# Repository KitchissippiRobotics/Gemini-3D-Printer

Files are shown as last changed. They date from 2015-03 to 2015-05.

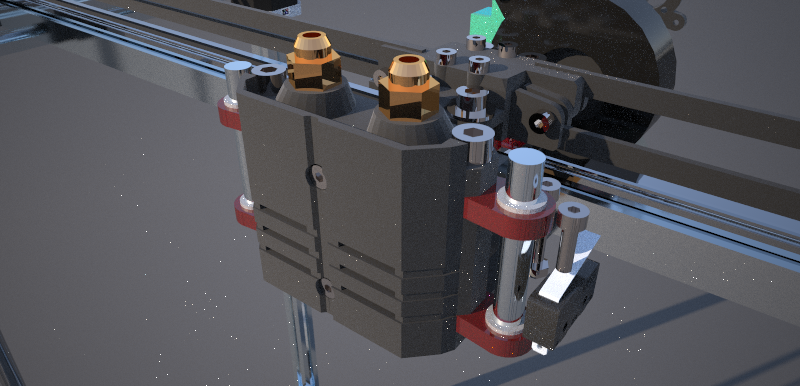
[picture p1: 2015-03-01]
Test Renderings/Development Mockup HA.05.1.png

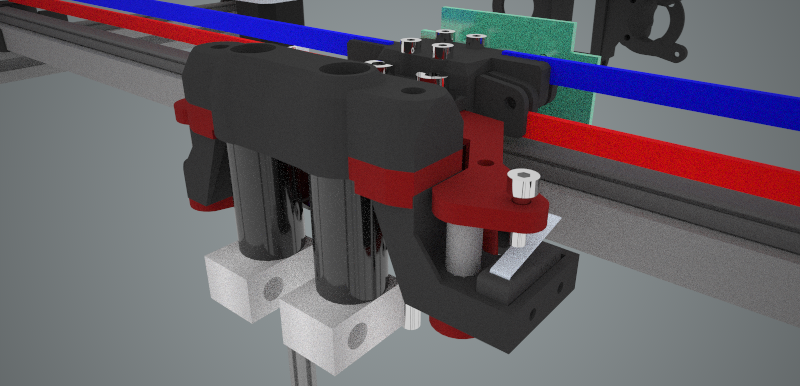
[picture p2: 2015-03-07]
Test Renderings/Development Mockup - Proof of Concept Preview.png

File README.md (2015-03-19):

# Gemini-3D-Printer
<h1>CoreXY RepRap Style 3D Printer</h1>

This is a test bed for experiments aiming for a large 300mm X 300mm X 400+mm print area FFF (layered filament) 3D printer.

<h2>Project Status and Description</h2>

This is an in-progress design for the machine - the source may change frequently and is not currently stable.
Any questions can be directed to novakane on the freenode IRC channel #reprap 

Initial object models were designed to minimize initial print time; test the underlying design theory; and finally, identify stress points in assembly.
This makes the parts more fragile than a production model, however the initial K02.2 prototype successfully made several prints of decent quality.
Most print failures may have been explained by early bed mounting and filament pusher mounting - these were done mostly as hacks to test the electronics and basic mechanism.

<h2>History Notes</h2>

This project is the developers second CoreXY design and 5th original 3D printer design.

- The first version - several revisions of the K02.1 - was based around an experimental carriage for movement using low cost materials
- The first version was abandoned due to required materials being made of large lengths of steel; while fully functional, the machine was heavier than ideal
- Carriages formed the basis of the successful K03.1 and K03.2 prototype delta machines, intended as outlets for recycling initial K02 materials, fully functional but incomplete at this writing.
- Cost analysis revealed that the original K02 (and perhaps K03) was not providing significant savings in cost vs production effort 
- production of the K02/K03 machines accurately requires machinery exceeding any savings - they can be built with simple tools like a punch/hand-drill/hacksaw, but great care must be taken (mass replication would be difficult)

<h2>Work Notes</h2>

This project is the developers second CoreXY design and 5th original 3D printer design.

- The first version - several revisions of the K02.1 - was based around an experimental carriage for movement using low cost materials
- The first version was abandoned due to required materials being made of steel; while fully functional, the machine was heavier than ideal
- Carriages formed the basis of the successful K03.1 and K03.2 prototype delta machines, intended as outlets for recycling initial K02 materials, fully functional but incomplete at this writing.
- Cost analysis revealed that the original K02 (and perhaps K03) was not providing significant savings in cost vs production effort 
- production of the K02/K03 machines accurately requires machinery exceeding any savings - they can be built with simple tools like a punch/hand-drill/hacksaw, but great care must be taken (mass replication would be difficult)

<h2>Development Notes</h2>

*19/March/2015* Hotend Chassis now merged into the Master. Starting work on finalizing rest of X carriage.

<h2>Incomplete BOM</h2>

<h3>Hardware and Electronics</h3>

<h2>Incomplete BOM</h2>

- (5) 20mm X 20mm x 500mm aluminum slotted extrusions (20x20 at half meter lengths) for horizontal dimensions
- (4) 1000mm for vertical segments {(4) 250mm length cut from ends to form part of the base
- (16) F694ZZ bearings for idlers
- (2) GT2-20 pulleys for drive motors
- (2) 50:1 geared NEMA17 motors for extruder pusher
- (2) 8mm ID x 13mm OD hobbed pulley with groove
- (4) Pneumatic pushfit connectors
- (2) ?? length of PTFE Tube 2mm ID x 4mm OD for bowden drive
- (4) 12mm x 500mm hardened steel rod for Z axis linear guide
- (4) LM12UU bearings for Z axis linear guide
_ (150?) M4x10mm allen head steel bolts
- (100?) M3x10mm allen head steel bolts
- (2) M4x?? hex head bolts for Y axis idlers
- (2) M4x?? hex head bolts for Y axis idlers
- (4) M4x50mm allen head steel bolts for Hotend Assembly mount to X Carriage
- (3) MGR9 x 500mm linear rails for CoreXY linear guides
- (3) micro switches for endstops
- (1) 24v 15A 360W power supply
- (1) Smoothieboard for controller
- (2) 12v 0.1A 25mm DC fan for bent cooling on hotends
- (2) jhead hotends 0.4mm nozzle
- (1) 12v 0.06A blower fan

<h2>Voltage converters for inputs to controller from 24v PSU</h2>

24v in - heatbed, hotends, motors
12v in - fans in Hotend assembly / X Carriage / Electronics Assembly (keep under 2 amp)
5v  in - USB/ethernet/CPU power (USB equivalent draw) (keep under 1 amp)

<h2>About the Developer</h2>

- "I am not an engineer, but I play one on the Internet"
- I have played many roles in my life, I am a software developer, an artist, an animator, a musician, a labourer, a technical analyst, a network engineer, an electronics engineer, an educator, a lover, a fighter.
- I am a jack of all trades, a traveller of life and today - I am a roboticist.
- I can be found on #reprap IRC as "novakane"
- I am attempting to bring together what little I know of mechanics, assembly, and avionics into a cohesive 3D printing platform

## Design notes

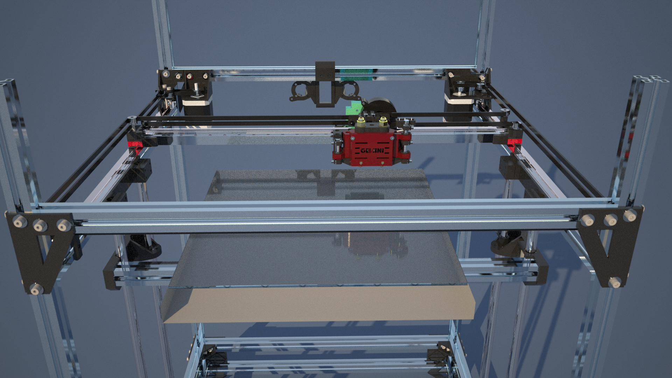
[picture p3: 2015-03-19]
Test Renderings/Development Mockup - Overview.png

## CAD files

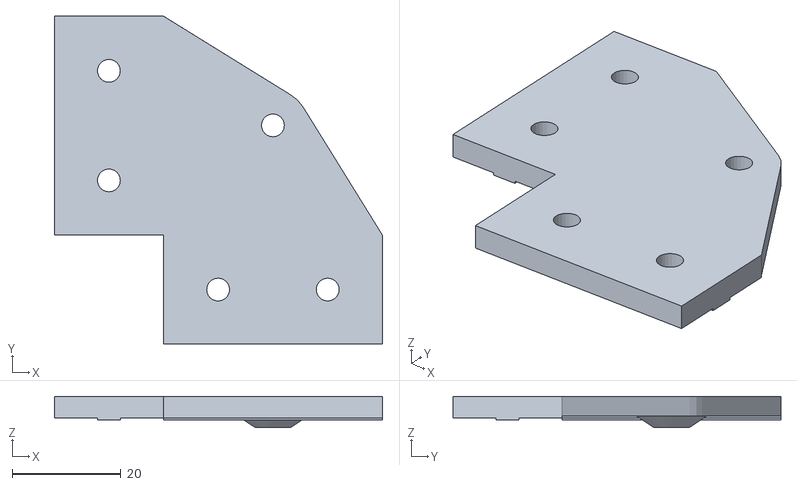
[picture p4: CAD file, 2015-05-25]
Print Models/Top Idler Corner.stl
60.3 x 60.3 x 5.79

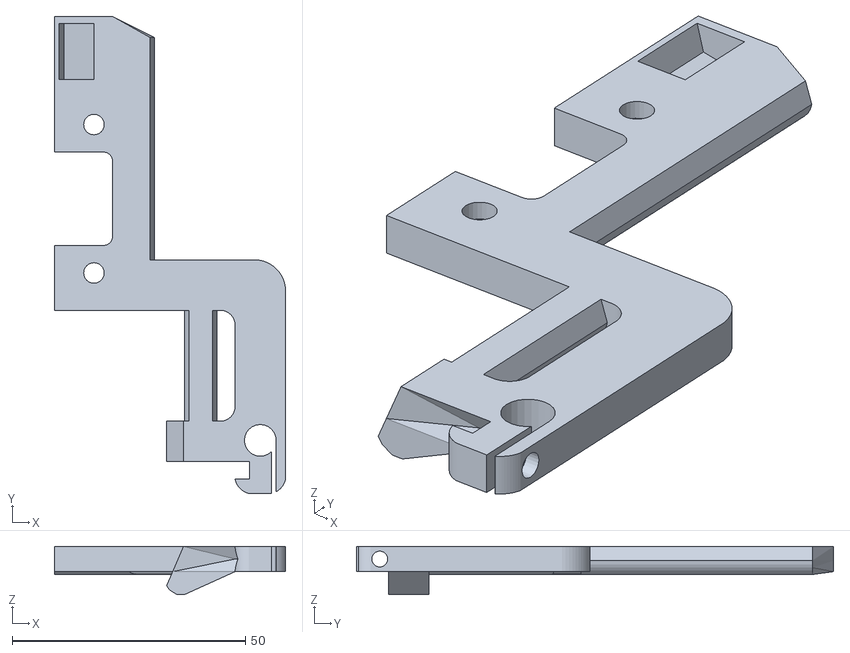
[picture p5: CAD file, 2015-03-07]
Test Models/Ducted Base Test.stl
49.5 x 102.2 x 10.3

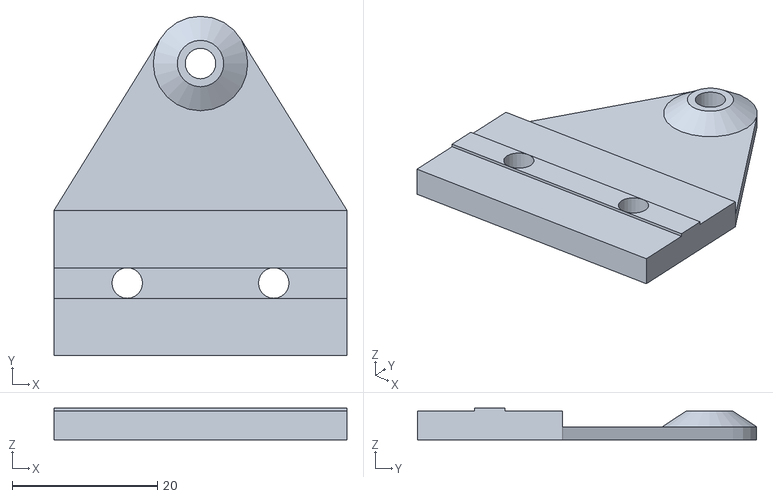
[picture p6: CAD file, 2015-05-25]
Print Models/Bottom Idler Corner.stl
40.3 x 46.7 x 4.40

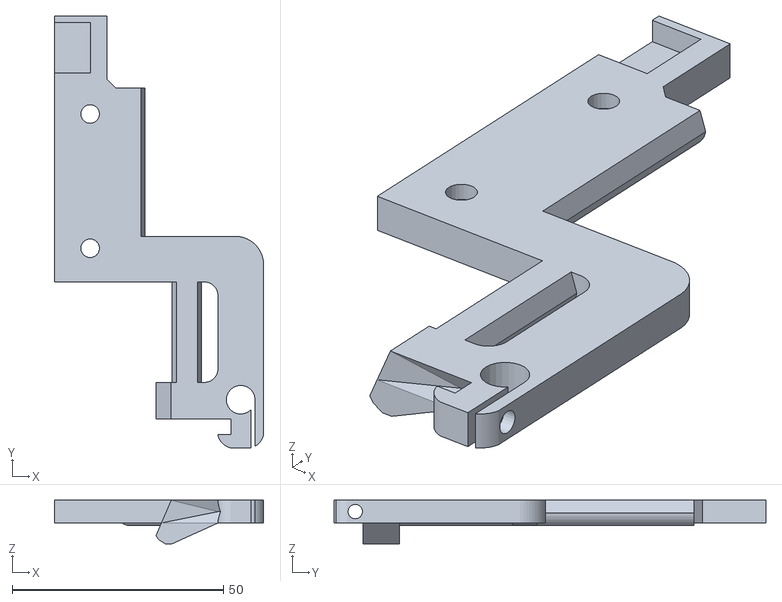
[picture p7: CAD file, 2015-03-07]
Test Models/Development Mockup.stl
49.5 x 102.2 x 10.3

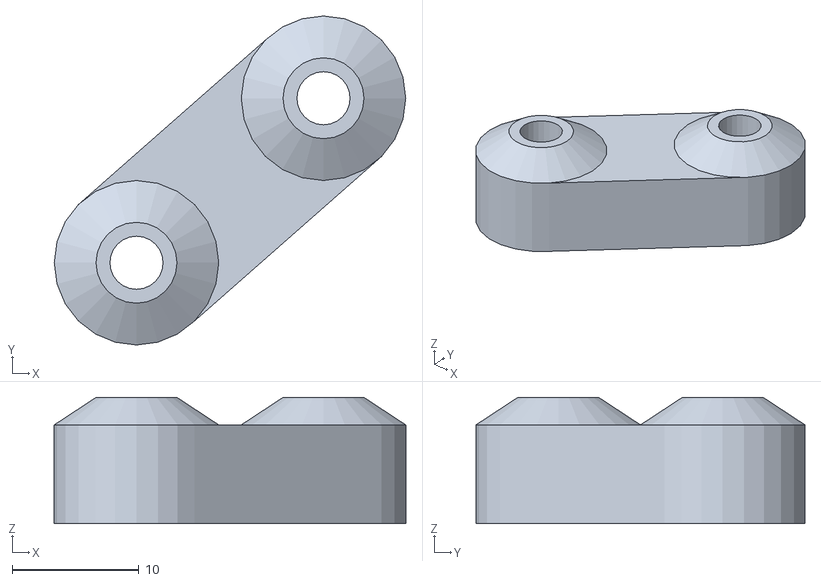
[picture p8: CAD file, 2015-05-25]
Print Models/X End - Pulley Support (x2).stl
27.8 x 26.0 x 9.97

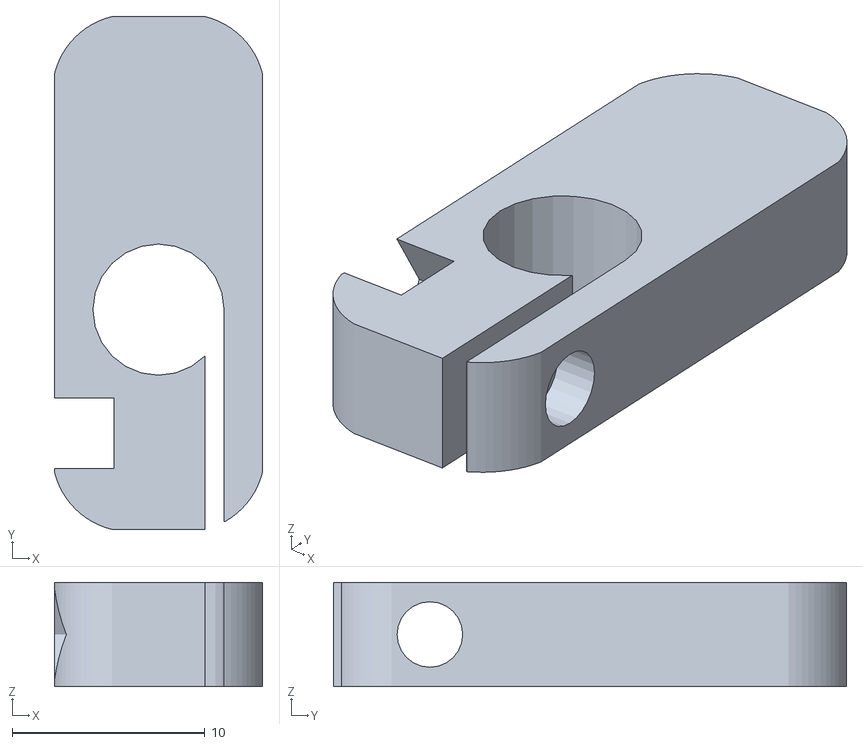
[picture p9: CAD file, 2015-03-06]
Test Models/Clamp.stl
10.8 x 26.6 x 5.40

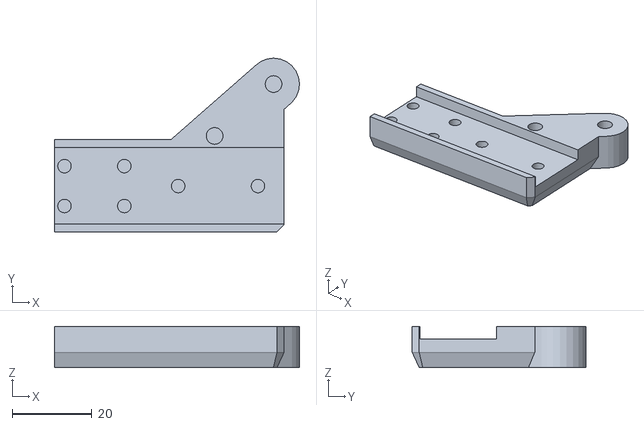
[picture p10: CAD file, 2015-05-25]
Print Models/X End - Left Base.stl
61.4 x 43.5 x 10.3

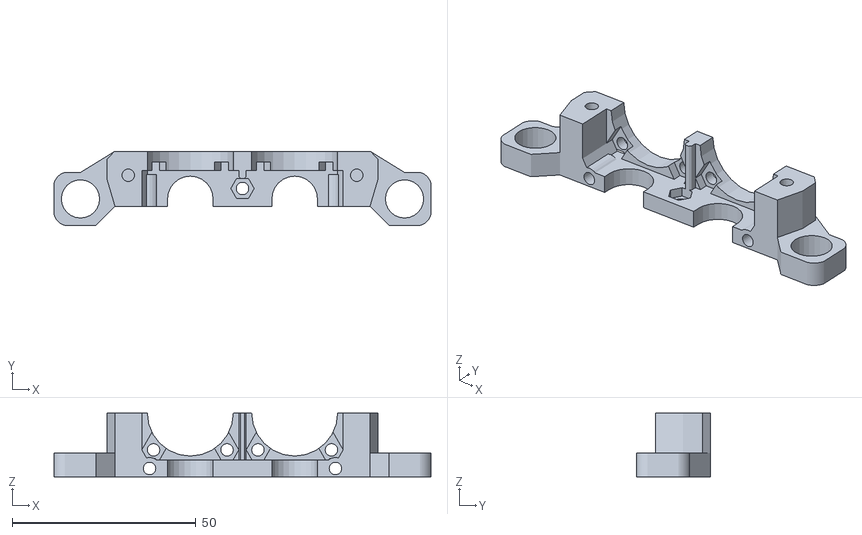
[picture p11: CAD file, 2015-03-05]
Test Models/Beefcake Mount.stl
102.6 x 20.1 x 17.4

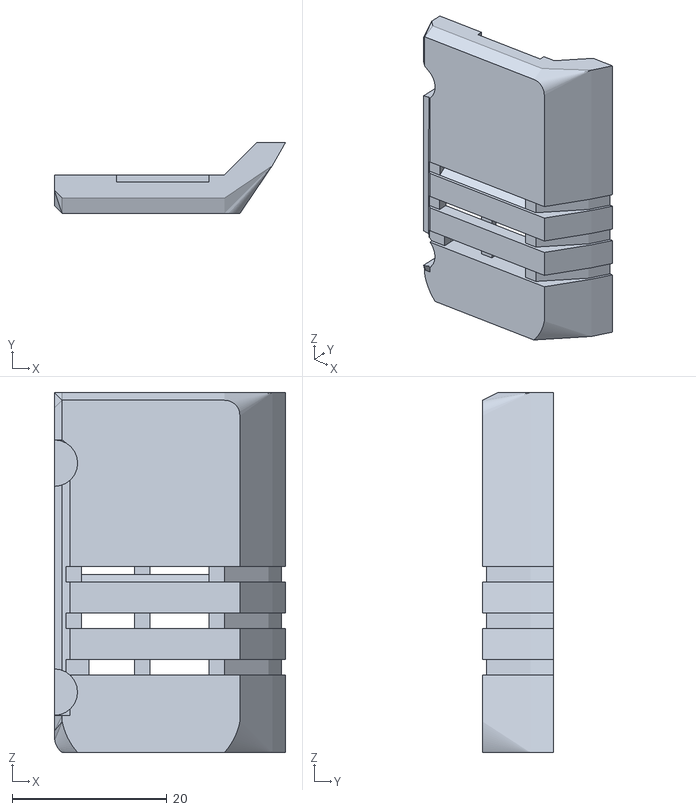
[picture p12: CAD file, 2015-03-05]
Test Models/Vent Cover.stl
29.9 x 9.19 x 46.5

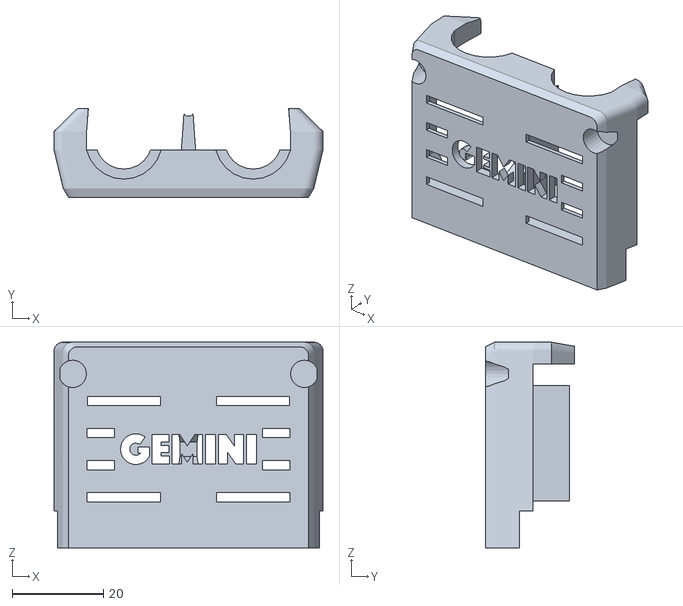
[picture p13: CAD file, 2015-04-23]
Print Models/Hotend Chassis - Groovemount Cover.stl
58.8 x 19.4 x 44.9

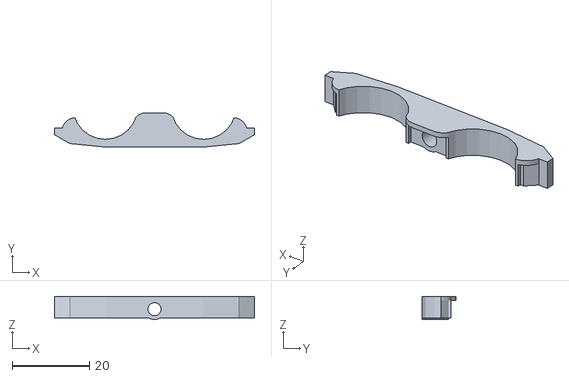
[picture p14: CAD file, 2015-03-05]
Test Models/HA Lower Clamp.stl
51.9 x 8.86 x 6.00

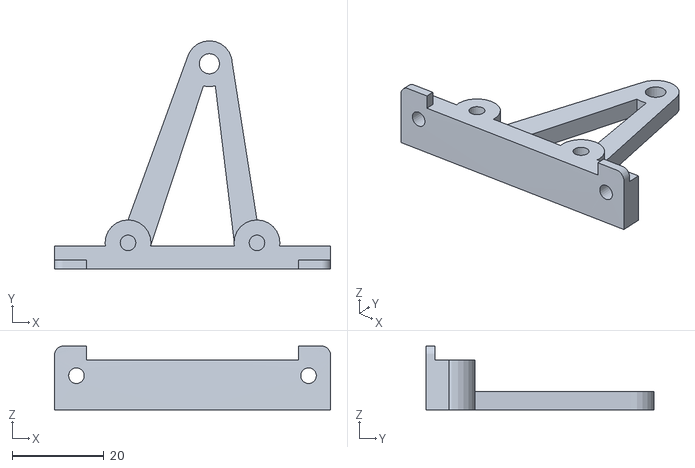
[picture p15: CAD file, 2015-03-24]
Print Models/X Carriage - Terminal Mount.stl
60.0 x 49.7 x 13.9

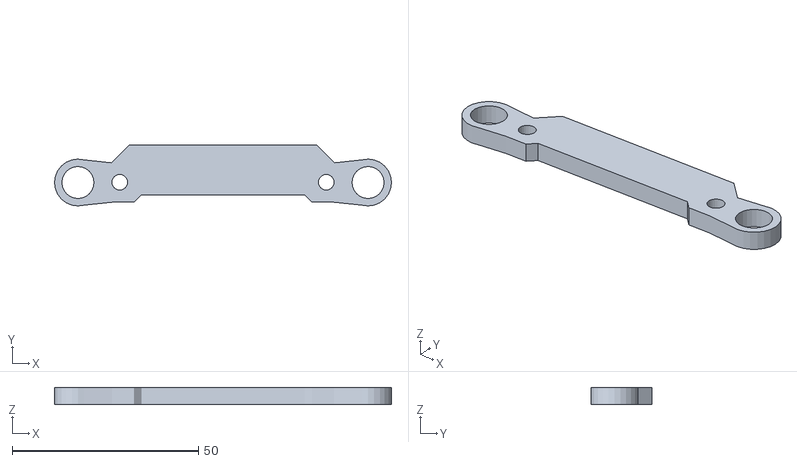
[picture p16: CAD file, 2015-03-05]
Test Models/HA Cross Bar.stl
90.6 x 16.4 x 4.60

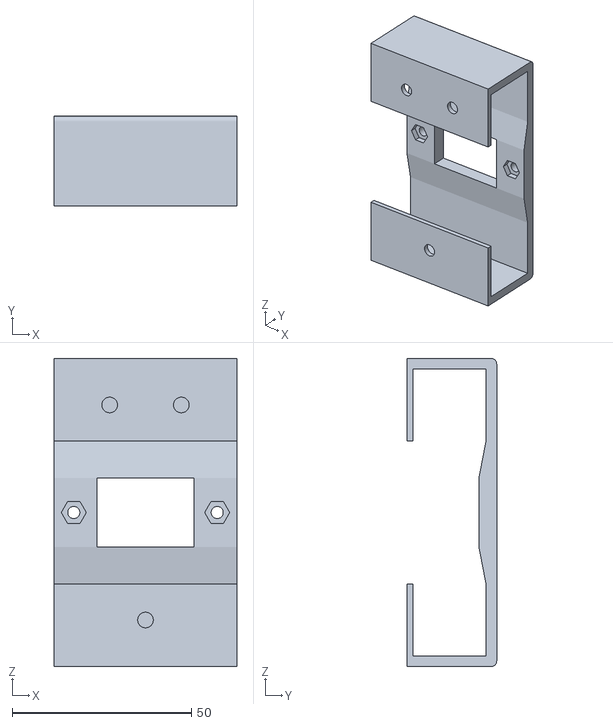
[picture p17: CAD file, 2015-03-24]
Print Models/Frame - AC Plug Mount.stl
51.0 x 25.0 x 85.9

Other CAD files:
Print Models/X End - Right Base.stl
Test Models/Fan Mount.stl
Print Models/X Carriage - Bottom Belt Clamp.stl
Test Models/HA Lower Support.stl
Print Models/Extruder - Pusher Mount Left.stl
Print Models/Extruder - Pusher Mount Right.stl
Print Models/Frame - Top Corner Brace (Print Eight).stl
Print Models/Gantry - Front Idler (Print Two).stl
Print Models/Gantry - Left Motor Mount.stl
Print Models/Gantry - Rear Left Idler.stl
Print Models/Gantry - Rear Right Idler.stl
Print Models/Gantry - Right Motor Mount.stl
Print Models/Hotend Chassis - Bottom Frame.stl
Print Models/Hotend Chassis - Bowden Cap.stl
Print Models/Hotend Chassis - Pushfit Retainer.stl
Print Models/Hotend Chassis - Slide Bushing.stl
Print Models/Hotend Chassis - Top Frame.stl
Print Models/Hotend Chassis - Z Probe Clamp.stl
Print Models/X Carriage - Bottom Mount.stl
Print Models/X Carriage - Rear Mount.stl
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

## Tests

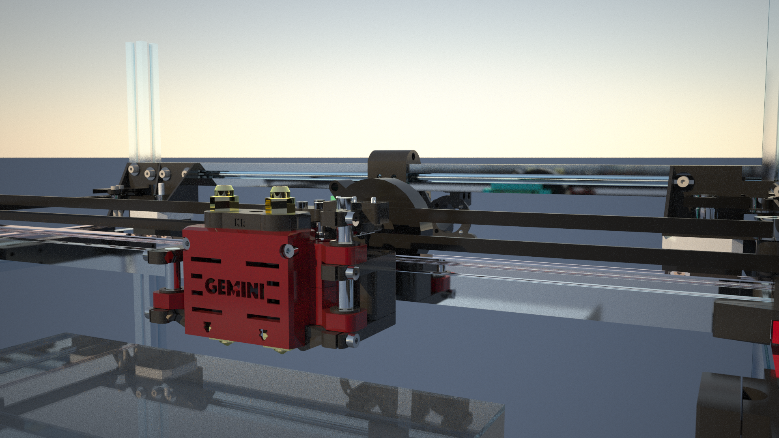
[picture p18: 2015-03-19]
Test Renderings/Development Mockup - Gantry Angled.png

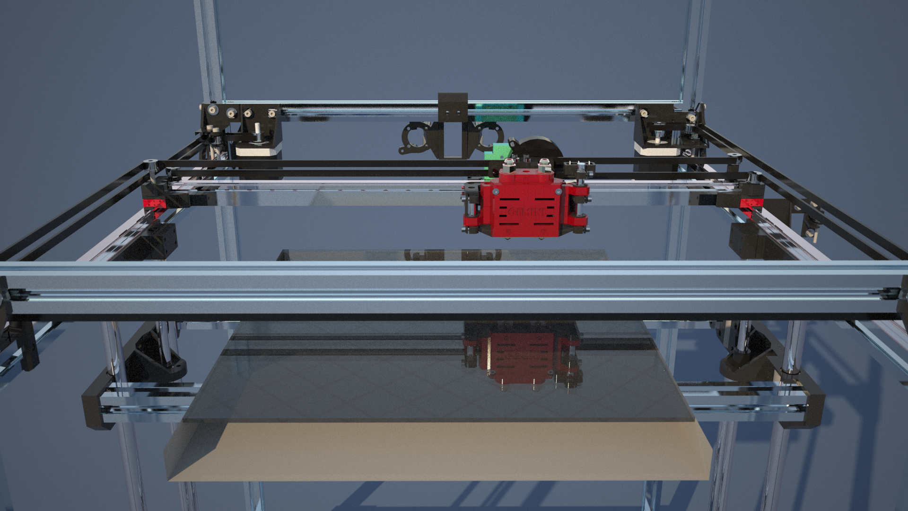
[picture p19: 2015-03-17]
Test Renderings/Development Mockup - Gantry.png

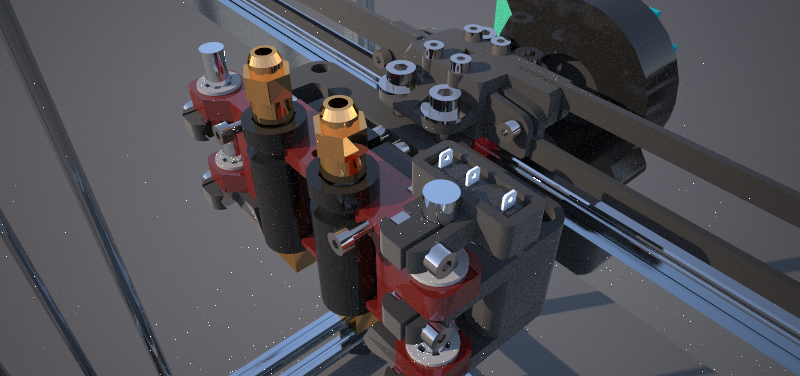
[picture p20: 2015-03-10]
Test Renderings/Development Mockup HA.06-NoCover.png

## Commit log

2015-02-22 X Carriage Print Models
    [X Carriage Bottom.stl, X Carriage Centre.stl, X Carriage Top.stl]
2015-02-22 Y Carriage Parts
    [Y Carriage Bottom.stl, Y Carriage Left Top.stl, Y Carriage Right Top.stl]
2015-02-22 Print Plates
    [Gantry - Front Idler (Print Two).stl, X Carriage - Bottom.stl, X Carriage - Centre.stl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]
2015-02-22 Hotend Assembly
    [Hotend Assembly - Bowden Retainer.stl, Hotend Assembly - Cap.stl, Hotend Assembly - Groove Mount.stl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]
2015-02-22 Parts Commit
    [Hotend Assembly - Left Strut.stl, Hotend Assembly - Lower Mount.stl, Hotend Assembly - Right Strut.stl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]
2015-02-22 Hotend Assembly Revision
2015-02-23 X Carriage Mods
2015-02-23 Crazy Hotend assembly and venting
2015-02-23 Interesting Design - Copper Tubes
    [Hotend Assembly - Lower Vents.stl]
2015-02-23 Rough Hotend Assembly Concept
    - attempt to strengthen assembly
    - attempt to compact the design
    - attempt to add ducting connection to back electronics assembly
    - revised switch alignment for Z endstop
    - slightly expanded slide bushing
    [Hotend Assembly - Lower Mount.stl, Hotend Assembly - Lower Vents.stl]
2015-02-24 Switch Position, styling, compactness
    [Hotend Assembly - Right Strut.stl]
2015-02-24 New Hotend Mount
2015-02-25 Rough Design of Hotend assembly moving carriage
2015-02-25 Revisions of Front Hotend Cover
    [Hotend Assembly - Left Strut.stl]
2015-02-28 MAC.04 Pre Split - Some parts
    [HA-03 Vents.stl, Hotend Assembly - Cap.stl]
2015-03-01 Bad ass looking hotend assembly
2015-03-02 Parts for Test Printing
    [HA-05 Vents.stl, Hotend Assembly - Cap.stl]
2015-03-03 Illusion Curves v1
    [Vent Cover.stl]
2015-03-05 Test Print Models
    [Fan Mount.stl, HA Cross Bar.stl, HA Lower Clamp.stl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]
2015-03-05 Beefcake. Beefcake!
    [Beefcake Mount.stl]
2015-03-05 Top and Bottom Pieces
    [Beefcake Mount.stl]
2015-03-06 Start of venting and x carriage mount
    [Hotend Assembly - Lower Mount.stl, Hotend Assembly - Upper Mount.stl]
2015-03-06 Switch test
2015-03-07 Z Clamp design & new bushings
    [Hotend Assembly - Bushing.stl, Z Endstop Clamp.stl]
2015-03-07 Duct work
2015-03-07 Partial Duct
2015-03-07 Ducted Base Testing
    [Development Mockup.stl, Ducted Base Test.stl]
2015-03-07 X Carriage Base for test printing
    [X Carriage Base.stl]
2015-03-10 HAC.06 Assembly Testing
    [X Carriage - Upper Mount.stl]
2015-03-10 HD Rendering of Gantry
2015-03-12 New Bowden Attachment
    [Hotend Assembly - Bowden Cap.stl, Hotend Assembly - Bowden Retainer.stl]
2015-03-14 3 Point Mod to HA
    [Hotend Assembly - Bowden Cap.stl, Hotend Assembly - Bowden Retainer.stl, Hotend Assembly - Retainer Face.stl]
2015-03-14 Print model cleanup
    [HA-03 Vents.stl, HA-05 Vents.stl, Hotend Assembly - Bowden Cap.stl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]
2015-03-14 New Model
    [Hotend Assembly - Groovemount Cover.stl]
2015-03-14 New Cover
    [Hotend Assembly - Groovemount Cover.stl]
2015-03-17 Commit from CLI
    [Hotend Assembly - Bowden Cap.stl, Hotend Assembly - Groovemount Cover.stl]
2015-03-18 Modfied Groovemount Cover
    [Hotend Assembly - Groovemount Cover.stl]
2015-03-19 Renamed Hotend Assembly as Hotend Chassis
    [Hotend Assembly - Bowden Cap.stl, Hotend Assembly - Bowden Retainer.stl, Hotend Assembly - Bushing.stl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]
2015-03-19 Hotend Chassis Updated
    [Hotend Chassis - Bottom Frame.stl, Hotend Chassis - Bowden Cap.stl, Hotend Chassis - Groovemount Cover.stl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]
2015-03-20 New Rear Carriage Mount
2015-03-20 New X Carriage - Bottom Mount.stl
    [X Carriage - Bottom.stl, X Carriage - Centre.stl, X Carriage - Top.stl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]
2015-03-21 Renamed Files
    [X Carriage - Bottom Belt Clamp.stl, X Carriage - Bottom Mount.stl, X Carriage - Rear Mount.stl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]
2015-03-24 PSU Parts
    [Hotend Chassis - Groovemount Cover.stl, X Carriage - Bottom Belt Clamp.stl, X Carriage - Rear Mount.stl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]
2015-04-23 Fixed Git Client?
    [Hotend Chassis - Groovemount Cover.stl]
2015-05-10 Exploring Frame Design
2015-05-10 Compacting Belt Path
    First revision of CoreXY configuration after taking a break
2015-05-10 Compact Simplified Gantry
    - uses four less pulleys
    - minimized gap between belt planes
    - separated Z axis ends from Y rail support
    - extraneous width on X carriage extends below belt path
    - more conducive to adding some top paneling
    - better view of print bed and hotends from front, less exposed belts
    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
2015-05-11 Did you see what they did to the pool?
    They flipped the b****! (Clone High)
    - flipped the layout of the belts to create a more open space along the
    front of the XY gantry
    - Minor adjustments of the belt location, still being tuned.
2015-05-11 Rough approximation of y end
    - multiple pieces that get assembled with a couple of bolts
    - added extra idler bearings which take no strain but avoids the long
    side belt having to rub against the support post
    - considering adding 2nd no-strain idler on other side of Y end
2015-05-12 Working on Y end Left
    - removed extraneous extra idler added on trailing edge
    - start of idler bearing connection points
    - beefed up idler housing
2015-05-13 Playing with ideas for gantry still
2015-05-14 Playing with gantry ideas
2015-05-14 Interesting Pulley Position for CoreXY
2015-05-14 X axis tilted 90 degrees forward
2015-05-15 Start of x carriage and belt clamping mount
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2015-05-21 Flipped X axis and changed support plate
2015-05-22 Split Left X End / Added mount holes
    - bolt holes for pulleys, hiwin mount, hiwin rail
    - split into two pieces for printability and assembly
    - test printing these two pieces now
    [X End - Left Base.stl, X End - Left Pulley Support.stl]
2015-05-24 More polished X end - right model added and test printing
    [X End - Left Base.stl, X End - Left Pulley Support.stl, X End - Pulley Support (x2).stl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]
2015-05-25 Modified x-ends
    [X End - Left Base.stl, X End - Right Base.stl]
2015-05-25 New Idlers
    [Bottom Idler Corner.stl, Top Idler Corner.stl, X End - Pulley Support (x2).stl]
